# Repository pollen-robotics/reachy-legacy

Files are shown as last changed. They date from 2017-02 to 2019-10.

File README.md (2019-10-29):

# Reachy the Bio-Inspired Robotic Arm

**Beautiful, Easy-to-use, Versatile, Open Source Human-size robotic arm for your robotic applications!**

## About
Reachy is a unique robot arm with a high level of mobility (7-Dofs). Different tool can be added on the arm's tip such as hook, gripper and 5 fingers hand.
You can learn more about this project on [its webpage](https://www.pollen-robotics.com/en/our-products/reachy/) and on youtube:
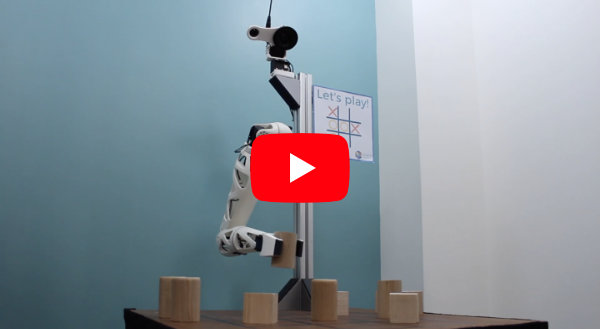
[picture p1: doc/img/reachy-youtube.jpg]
Video preview (https://www.youtube.com/watch?v=wsCYkz-BHyA&list=PLoZg6JOJfhpCa1Sy3cM4FOFkcFUBElqBF&index=2)


Reachy is designed and produced by Pollen Robotics, we offer product design and custom developpement, you can learn more on our [website](https://www.pollen-robotics.com/).

## Open source
Reachy hardware and software are both open source and can be freely modified/custumized by the end user to fit its needs.

The software is built on top of the [Pypot library](https://github.com/poppy-project/pypot) and is distributed under LGPL Licence.

The hardware is made using OnShape under [Creative Commons BY-SA licence](https://creativecommons.org/licenses/by-sa/4.0/) licence and is accessible [here](https://cad.onshape.com/documents/66388ae9c63cef53d76acd77/w/68c2411483d5bc65c7f54234/e/581d46ba9b8ee98de9d636ee)

## Documentation
In this repository, there are multiple examples explaining how to use reachy.

- A Quickstart on how to plug and start reachy can be found [here](./doc/readme.md).
- You can learn more on the software architecture [here](./doc/reachy-software-presentation.ipynb).
- Several examples are available in the folder [applications](./applications/).

Those notebooks can be viewed directly on GitHub or can also be run locally to directly experiment with your robot. See the [jupyter documention](https://jupyter.org) for mor information on how to do that.

## Installation

Reachy's control library is written in Python (>=2.7 or >= 3.4) and works on Win/Mac/Linux and Raspberry Pi. It allows for fast and simple control of your robotic arm. And also provides you example with more advanced features such as inverse kinematics, simulation, tracking, etc. It relies on the [pypot library](https://github.com/poppy-project/pypot) for the dynamixel motor communication.

On Raspberry-Pi, you can burn a ready to use image file (installation for both Python2 and Python3): [here](https://github.com/pollen-robotics/reachy/releases). You will need a 16Go SD card. 
You can plug a screen and keyboard directly on the Raspberry Pi or you can access it via ssh (hostname *reachy*, user *pi* and password *reachy*).

It can be installed from the source via pip.

```
git clone https://github.com/pollen-robotics/reachy.git
pip install -e ./reachy/software
```

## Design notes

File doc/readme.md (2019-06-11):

# Quickstart with Reachy

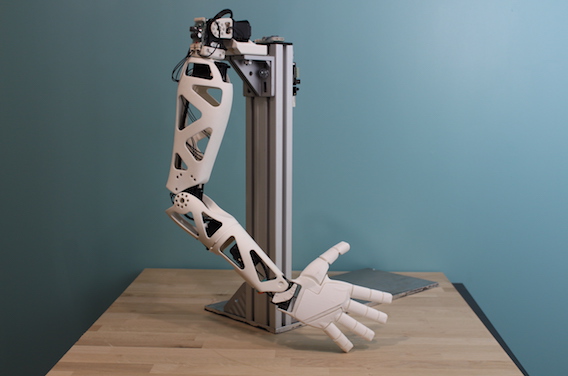
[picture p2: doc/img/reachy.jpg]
Reachy


## Plug your Reachy

The first step to start your Reachy robot is to make sure the motors are powered using the **two dedicated 12V power supply**. The usb dongle used to connect to the motors should be plugged to your computer or the Raspberry Pi.

See the pictures below for details.

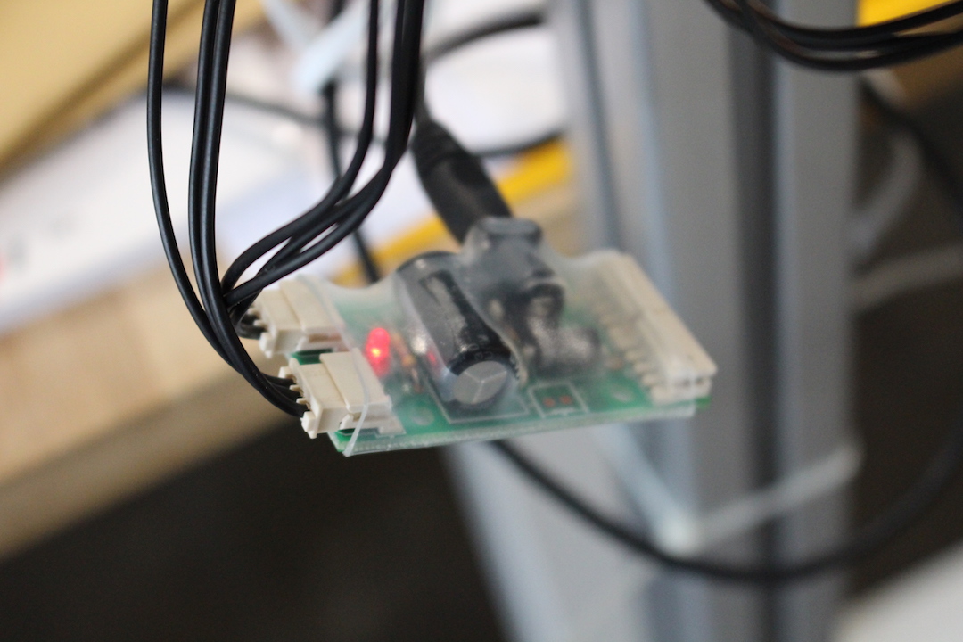
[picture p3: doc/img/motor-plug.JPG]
Motor plug

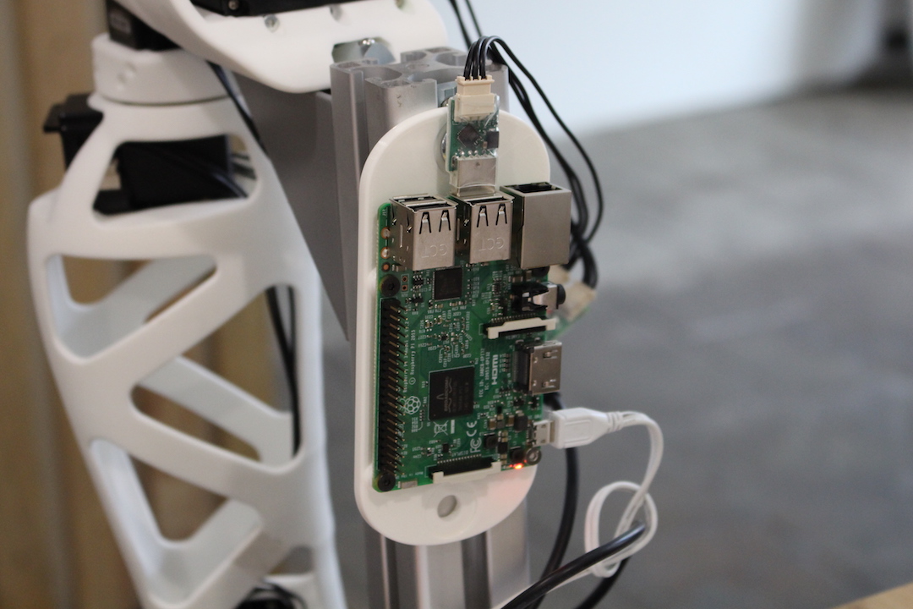
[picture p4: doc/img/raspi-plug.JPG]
Raspberry plug


Depending on the end-effector you are using, you may also need to plug it. For instance, also plug the dedicated USB if you are using the gripper with the force sensor.

## Software

The control libraries used for Reachy are all written in Python and can be directly found in this repo. A complete presentation can be found [here](./reachy-software-presentation.ipynb). You can also read the [Quickstart](./notebook/Reachy-Quickstart.ipynb) to directly jump in controlling reachy.

Most of the documentation can be found as jupyter notebook. Make sure to check [their documentation](https://jupyter.org) if you are unfamiliar with them. They are a really powerful way to document and let you experiment code.
You will find them in two main places:

* the basic ones for a general presentation can be found [here](./notebook).
* the specific ones with which are more applications oriented can be found [here](../applications)

## Safety First

Using a Reachy is not complex but at first it is easy to get confused. Most of the times it is not a big deal but some of the incorrect uses may easily damage it. There are a few pitfalls to avoid that, that can really help you at the beginning.

We strongly recommend you to have a look at the [safety first notebook](Safety-first.ipynb) to make sure everything goes well with your robot. By following these simple rules, you will be able to have your robot running without problem.

## FAQ & Troubleshooting

* Most of the connection problem with the robot are due to broken or badly plugged motor wires. Make sure to check them when you have trouble controlling your robot.

* Make sure to set the motor to not compliant before trying to move them! Otherwise they will simply do nothing.

* You can find more information on the documentation of the poppy project: https://docs.poppy-project.org/
 Most code should also work for the Reachy robot.

## Appendix - Using the Raspberry-Pi webinterface

### Connect to the robot interface

Once the robot is started, you can connect to its web interface. You can directly access it on http://reachy.local/ (This uses the zeroconf protocol to resolve the hostname. It should directly works on Linux and OS-X but requires to install this on Windows: https://support.apple.com/kb/DL999 You can also directly use the robot's IP if you know it).

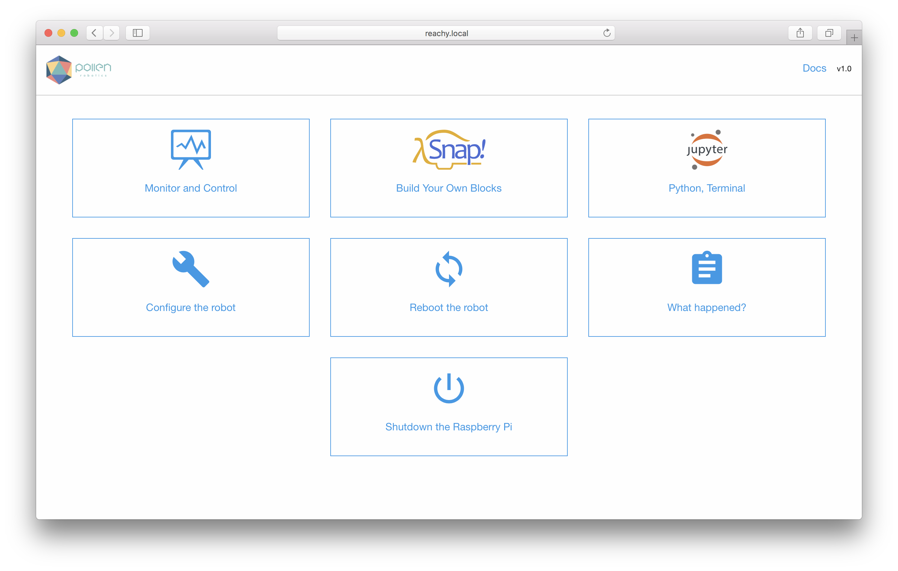
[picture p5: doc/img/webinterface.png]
Reachy web interface


 This lets you to use the monitor interface, directly run Python code in your robot using Jupyter or use the visual language Snap.

 You can find an example of Python code to start making your robot move in Jupyter.

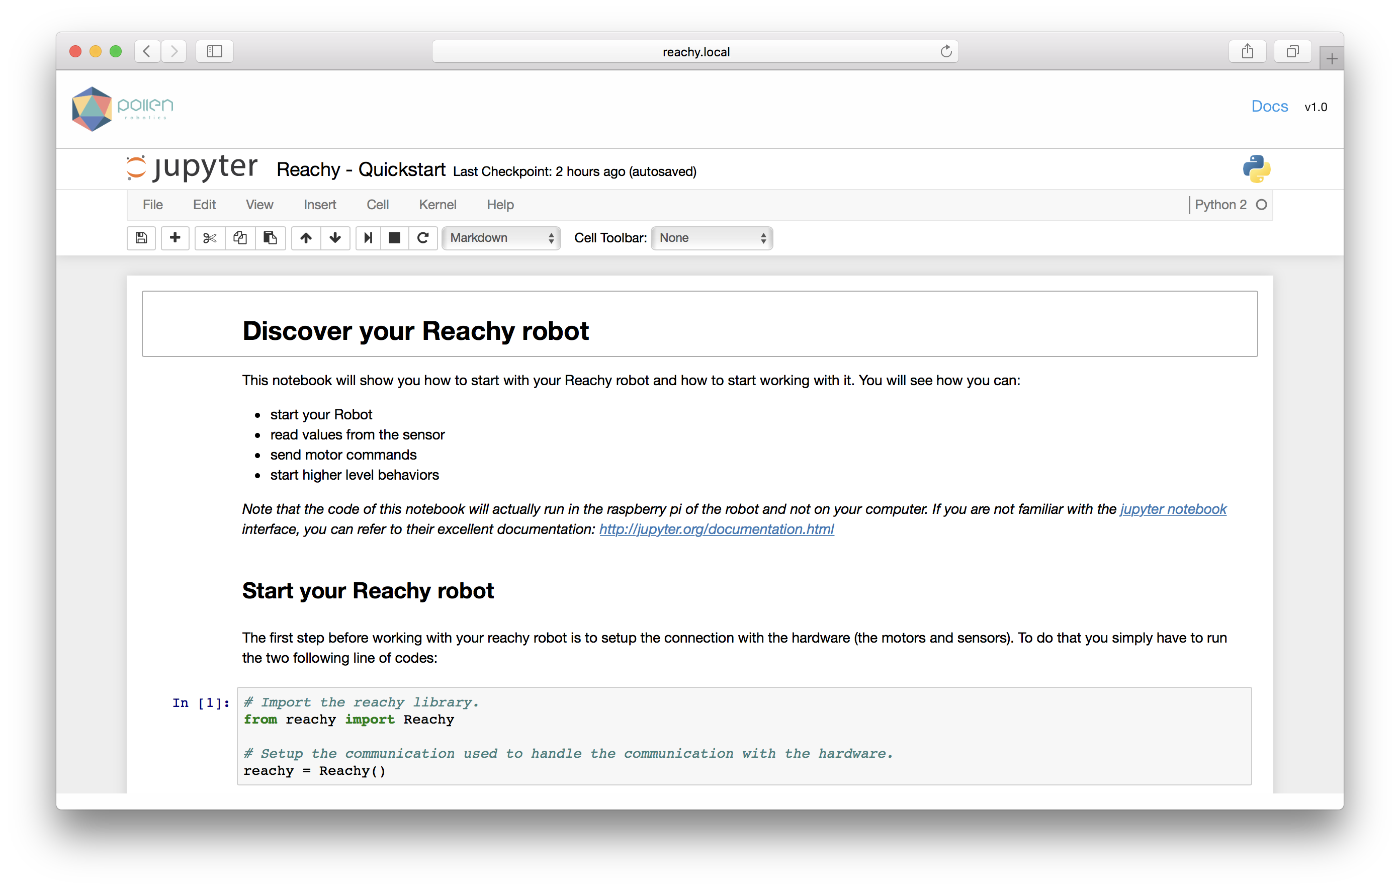
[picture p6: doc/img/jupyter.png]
Reachy jupyter example


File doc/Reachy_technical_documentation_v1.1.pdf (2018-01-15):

REACHY technical documentation

## REACHY TECHNICAL DOCUMENTATION

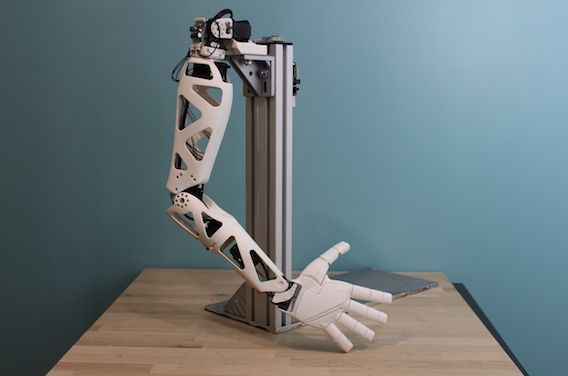
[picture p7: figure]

REACHY technical documentation

REVISIONS

Date | Revision | Author(s) | Comment(s)
22/11/2017 | 1.0 | Simon BAUDRY | First draft. Work in progress
15/01/2018 | 1.1 | Simon BAUDRY | New dimension specs.

REACHY technical documentation

# SUMMARY

### 1. Introduction

### 2. General specifications

### 3. Joints’ specifications

### 4. Dimensions

### 5. Initial position

### 6. Joints’ rotation

### 7. Servo-motors’ specifications

REACHY technical documentation

# 1.Introduction

Reachy is a full-size 7-dof prosthetic robotic arm. It can be programmed intuitively by demonstration or via an easy-to-use programming library.
It provides direct and inverse kinematics.

REACHY technical documentation

# 2.General specifications

Weight: ~1400 g

Height: ~660 mm to ~800 mm (according to type of hand).

Degrees of freedom: 7

Power requirement:
Minimum one power supply 12V 5A. Suggested two power supplies 12V 5A (one for the upper motor in the shoulder, one for the other motors in the arm).

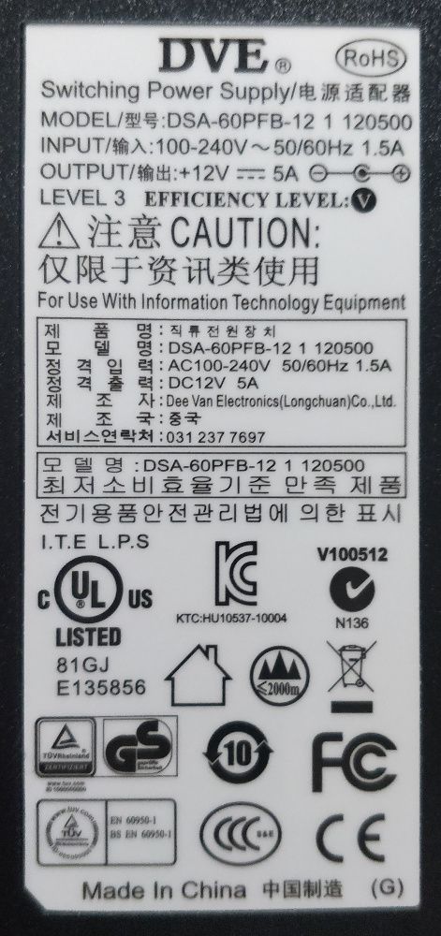
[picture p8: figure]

REACHY technical documentation

Payload:
WIP

Fixation method:
The arm can be fixed to a T-slotted bar.

Reproducibility of movements and delta: WIP

REACHY technical documentation

# 3.Joints’ specifications

Reachy is divided in 5 parts and 7 joints.

A part is composed of an actuator and a shell. Parts are roughly the same than in human body (e.g. shoulder, wrist, …).
A joint is the location where a motion is allowed (e.g. rotation point between forearm and wrist); each joint is associated to a degree of freedom.

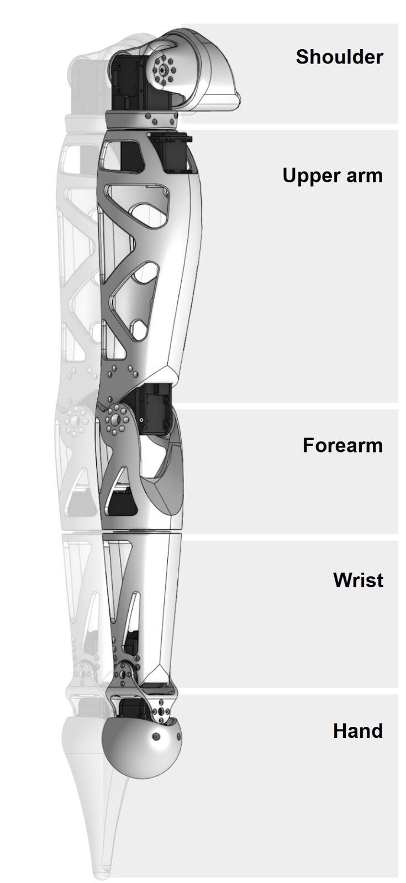
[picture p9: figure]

REACHY technical documentation

# 4.Dimensions

Dimensions on the top in the figure X and left of the figure Y below are provided from one rotation point (joint) to another. Dimensions on the bottom and on the right are general maximal dimensions (according to two different types of hand).

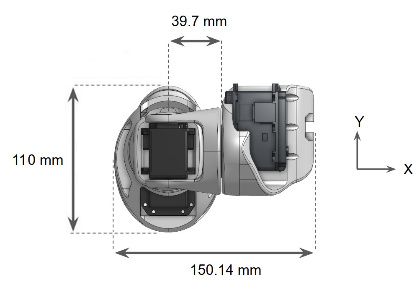
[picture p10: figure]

REACHY technical documentation

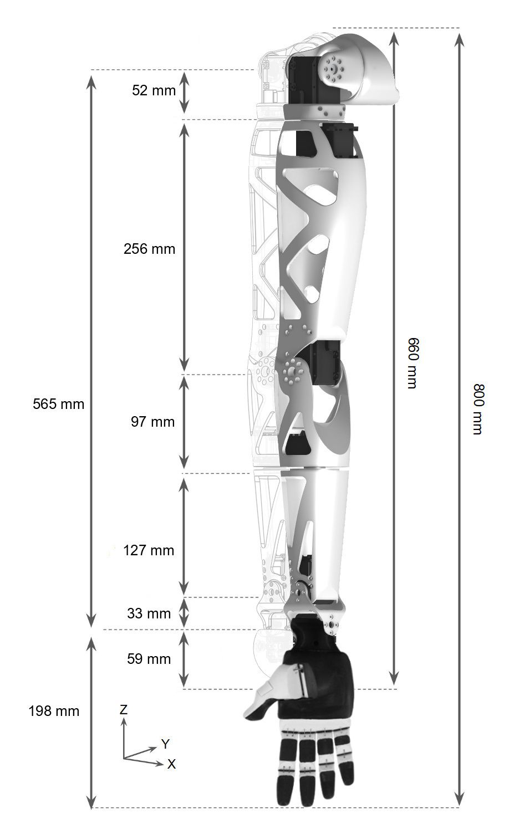
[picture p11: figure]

REACHY technical documentation

# 5.Initial position

Reachy’s initial position is as shown:

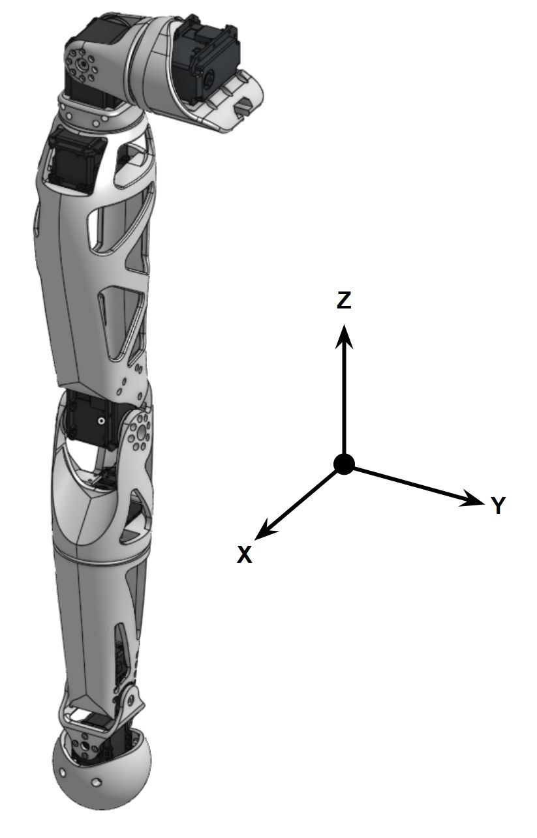
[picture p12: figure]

REACHY technical documentation

# 6.Joints’ rotation

Each joint rotates around an axis, based from 0-position of Reachy. A rotation around X axis is called Roll, a rotation around Y axi is called Pitch, and a rotation around Z axis is called Yaw.

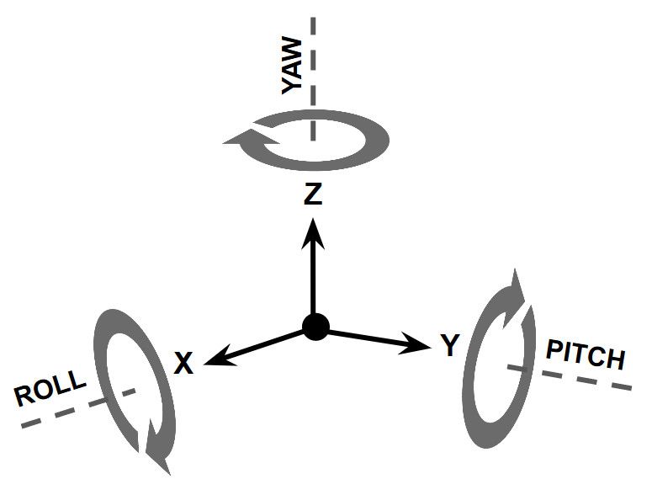
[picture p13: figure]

According to this, the joint’s names are composed of the place of the joint (shoulder, elbow, ...) and the rotation allowed (pitch, roll, or yaw). Each joint has a limited range angle (no endless rotation).

REACHY technical documentation

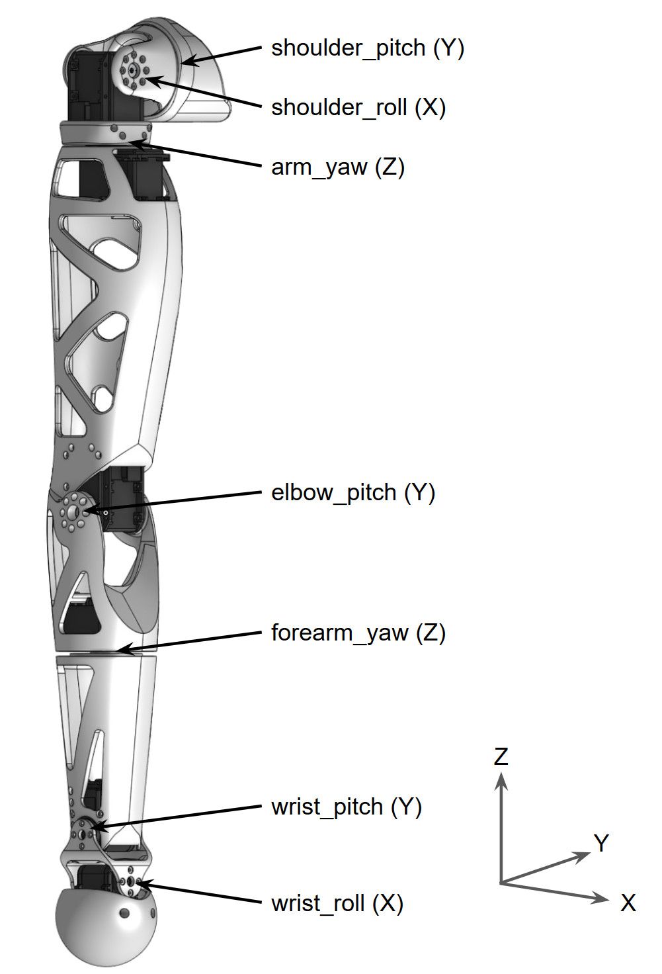
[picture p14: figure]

The following tables show servo-motors’ name, ranges of angles and initial angle of each joint.

REACHY technical documentation

| Right arm
Motor type | Origin angle ° | Min angle ° | Max angle °
shoulder_pitc h | MX-106T | -90 | -180 | 90
shoulder_roll | MX-64AT | -90 | -100 | 90
arm_yaw | MX-64AT | 0 | -90 | 90
elbow_pitch | MX-64AT | 0 | 0 | 125
forearm_yaw | AX-18A | 0 | -150 | 150
wrist_pitch | AX-18A | 0 | -70 | 70
wrist_roll | AX-18A | 0 | -60 | 60
| Left arm
Motor type | Origin angle ° | Min angle ° | Max angle °
shoulder_pitc h | MX-106T | -90 | -180 | 90
shoulder_roll | MX-64AT | -90 | -100 | 90
arm_yaw | MX-64AT | 0 | -90 | 90
elbow_pitch | MX-64AT | 0 | 0 | 125
forearm_yaw | AX-18A | 0 | -150 | 150
wrist_pitch | AX-18A | 0 | -70 | 70
wrist_roll | AX-18A | 0 | -60 | 60

REACHY technical documentation

# 7.Servo-motors’ specifications

Servo-motors are from the company Robotis, Dynamixel type.

| Resolution ° | Dimension LxDxH mm | Weight g | Running degrees ° | Reduction ratio | Link
MX-106T | 0.088 | 40.2x65.1x46 | 153 | 0-360, endless | 225 | TTL
MX-64AT | 0.088 | 40.2x61.1x41 | 135 | 0-360, endless | 200
AX-18A | 0.29 | 32x50x40 | 54.5 | 0-300, endless | 254
| Voltage | Stall torque (N.m) | No-load speed (RPM) | Stall current (A) | Standby current
Range (V) | (V) | 11.1V | 12V | 14.8V | 11.1V | 12V | 14.8V | 11.1V | 12V | 14.8V | mA Nominal
MX-106T | 10-14.8 | 12 | 8 | 8.4 | 10 | 41 | 45 | 55 | 4.8 | 5.2 | 6.3 | 100
MX-64AT | 10-14.8 | 12 | 5.5 | 6 | 7.3 | 58 | 63 | 78 | 3.9 | 4.1 | 5.2 | 100
AX-18A | 9-12 | 11.1 | - | 1.8 | - | - | 97 | - | - | 2.2 | - | -

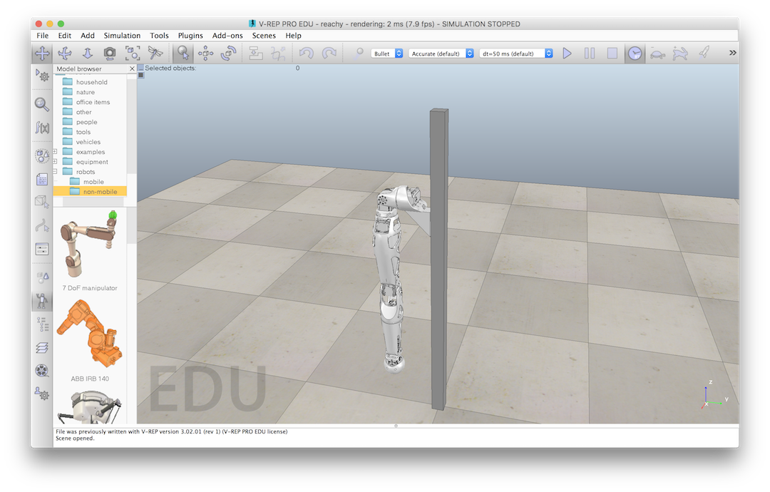
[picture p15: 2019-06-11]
doc/img/reachy-vrep.png

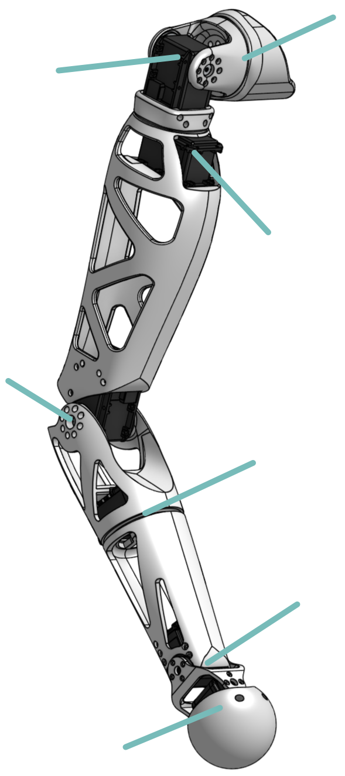
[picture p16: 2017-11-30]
assets/reachy.png

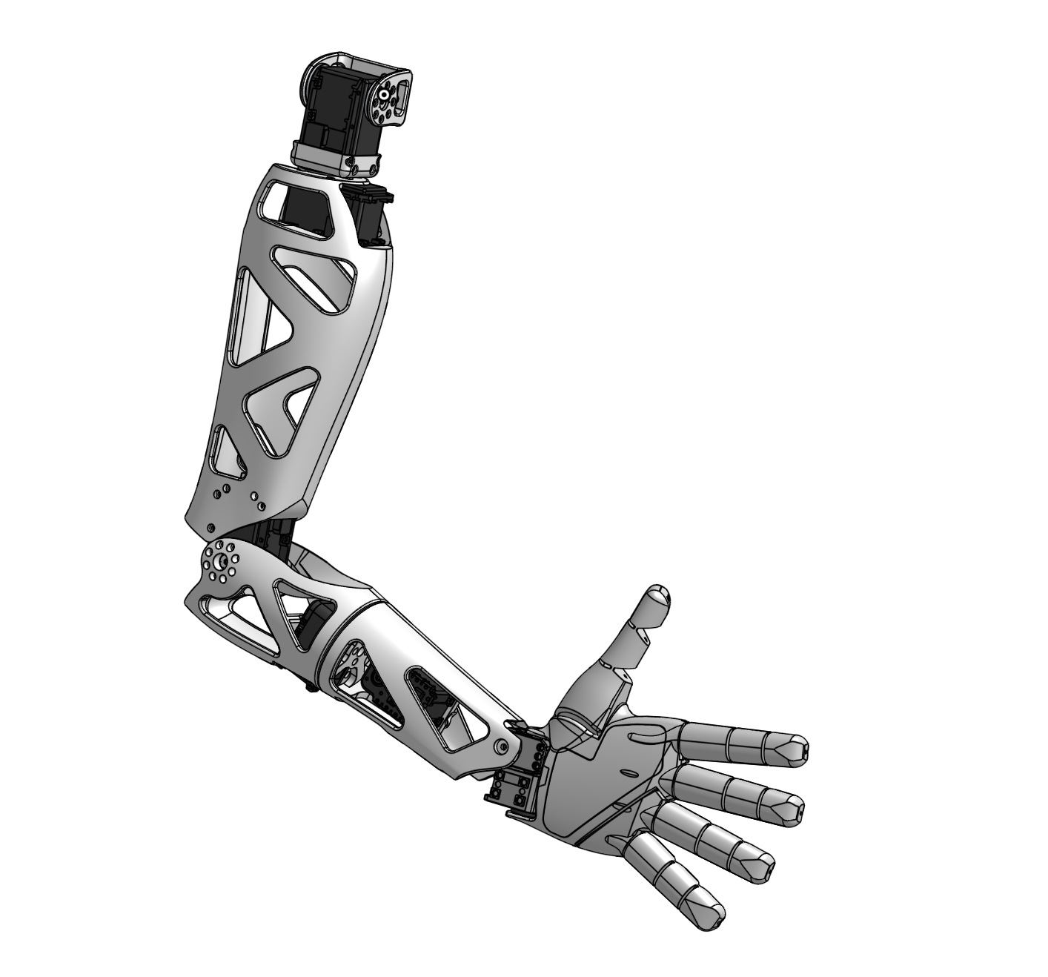
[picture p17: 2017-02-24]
doc/img/meca.png

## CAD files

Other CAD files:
hardware/URDF/meshes/trunk-respondable.stl
hardware/URDF/meshes/open_bionics_hand_left-visual.stl
hardware/URDF/meshes/open_bionics_hand_right-visual.stl
hardware/URDF/meshes/head_u-visual.stl
hardware/URDF/meshes/head-eyes-visual.stl
hardware/URDF/meshes/trunk-visual.stl
hardware/URDF/meshes/open_bionics_hand_left-respondable.stl
hardware/URDF/meshes/head-eyes-respondable.stl
hardware/URDF/meshes/open_bionics_hand_right-respondable.stl
hardware/URDF/meshes/shoulder-left-visual.stl
hardware/URDF/meshes/shoulder-y-left-respondable.stl
hardware/URDF/meshes/shoulder-y-left-visual.stl
hardware/URDF/meshes/shoulder-left-respondable.stl
hardware/URDF/meshes/forearm-respondable.stl
hardware/URDF/meshes/forearm-visual.stl
hardware/URDF/meshes/ball-tip-respondable.stl
hardware/URDF/meshes/shoulder-y-respondable.stl
hardware/URDF/meshes/wrist-hand-visual.stl
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

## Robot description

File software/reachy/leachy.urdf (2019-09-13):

<?xml version="1.0"?>
<robot name="Reachy">

  <material name="blue">
    <color rgba="0 0 0.8 1"/>
  </material>

  <material name="white">
    <color rgba="1 1 1 1"/>
  </material>

  <material name="red">
    <color rgba="0.8 0 0 1"/>
  </material>

<link name="base">
    <visual>
      <geometry>
        <mesh filename="package://meshes/shoulder-y-left-visual.STL"></mesh>
      </geometry>
      <material name="blue"/>
    </visual>
    <inertial>
      <inertia ixx= "1.043e-4" ixy= "6.147e-6" ixz= "-1.971e-6" iyy= "1.364e-4" iyz= "1.466e-5" izz= "1.403e-4" ></inertia>
      <mass value="0.221"></mass>
    </inertial>
    <collision>
      <origin xyz="0 0 0" rpy="0 0 0"></origin>
      <geometry>
        <mesh filename="package://meshes/shoulder-y-left-respondable.STL"></mesh>
      </geometry>
    </collision>
  </link>

  <link name="shoulder">
    <visual>
      <origin xyz="0 0 0" rpy="0 0 0"></origin>
      <geometry>
        <mesh filename="package://meshes/shoulder-left-visual.STL"></mesh>
      </geometry>
      <material name="white"/>
    </visual>
    <inertial>
      <inertia ixx= "1.299e-5" ixy= "5.557e-10" ixz= "-2.973e-10" iyy= "2.323e-5" iyz= "-8.199e-8" izz= "2.227e-5" ></inertia>
      <mass value="0.036"></mass>
    </inertial>
    <collision>
      <origin xyz="0 0 0" rpy="0 0 0"></origin>
      <geometry>
        <mesh filename="package://meshes/shoulder-left-respondable.STL"></mesh>
      </geometry>
    </collision>

  </link>

  <link name="shoulder_to_arm">
    <visual>
      <geometry>
        <mesh filename="package://meshes/shoulder-x-visual.STL"></mesh>
      </geometry>
      <origin rpy="0 0 0" xyz="0 0 0"/>
      <material name="blue"/>
    </visual>
    <inertial>
      <inertia ixx= "6.811e-5" ixy= "-2.299e-10" ixz= "-4.502e-7" iyy= "7.593e-5" iyz= "-1.674e-9" izz= "4.248e-5" ></inertia>
      <mass value="0.155"></mass>
    </inertial>
    <collision>
      <origin xyz="0 0 0" rpy="0 0 0"></origin>
      <geometry>
        <mesh filename="package://meshes/shoulder-x-respondable.STL"></mesh>
      </geometry>
    </collision>
  </link>

  <link name="upper_arm">
    <visual>
      <geometry>
        <mesh filename="package://meshes/upper-arm-visual.STL"></mesh>
      </geometry>
      <origin rpy="0 0 0" xyz="0 0 0"/>
      <material name="white"/>
    </visual>
    <inertial>
      <inertia ixx= "4.171e-3" ixy= "1.333e-7" ixz= "-2.900e-4" iyy= "4.276e-3" iyz= "1.465e-6" izz= "3.177e-4" ></inertia>
      <mass value="0.430"></mass>
    </inertial>
    <collision>
      <origin xyz="0 0 0" rpy="0 0 0"></origin>
      <geometry>
        <mesh filename="package://meshes/upper-arm-respondable.STL"></mesh>
      </geometry>
    </collision>
  </link>

  <link name="forearm">
    <visual>
      <origin xyz="0 0 0" rpy="0 0 0"></origin>
      <geometry>
        <mesh filename="package://meshes/forearm-visual.STL"></mesh>
      </geometry>
      <origin rpy="0 0 0" xyz="0 0 0"/>
      <material name="blue"/>
    </visual>
    <inertial>
      <inertia ixx= "1.724e-4" ixy= "-1.733e-8" ixz= "1.854e-5" iyy= "1.815e-4" iyz= "-4.191e-8" izz= "9.299e-5" ></inertia>
      <mass value="0.129"></mass>
    </inertial>
    <collision>
      <origin xyz="0 0 0" rpy="0 0 0"></origin>
      <geometry>
        <mesh filename="package://meshes/forearm-respondable.STL"></mesh>
      </geometry>
    </collision>
  </link>

  <link name="wrist">
    <visual>
      <origin xyz="0 0 0" rpy="0 0 0"></origin>
      <geometry>
        <mesh filename="package://meshes/wrist-visual.STL"></mesh>
      </geometry>
      <origin rpy="0 0 0" xyz="0 0 0"/>
      <material name="white"/>
    </visual>
    <inertial>
      <inertia ixx= "2.215e-4" ixy= "-2.163e-8" ixz= "-4.702e-6" iyy= "2.306e-4" iyz= "-6.577e-7" izz= "5.075e-5" ></inertia>
      <mass value="0.115"></mass>
    </inertial>
    <collision>
      <origin xyz="0 0 0" rpy="0 0 0"></origin>
      <geometry>
        <mesh filename="package://meshes/wrist-respondable.STL"></mesh>
      </geometry>
    </collision>
  </link>

  <link name="wrist_hand">
    <visual>
      <geometry>
        <mesh filename="package://meshes/wrist-hand-visual.STL"></mesh>
      </geometry>
      <origin rpy="0 0 0" xyz="0 0 0"/>
      <material name="blue"/>
    </visual>
    <inertial>
      <inertia ixx= "3.861e-6" ixy= "-2.805e-9" ixz= "-8.067e-8" iyy= "3.694e-6" iyz= "-7.689e-8" izz= "4.987e-6" ></inertia>
      <mass value="0.009"></mass>
    </inertial>
    <collision>
      <origin xyz="0 0 0" rpy="0 0 0"></origin>
      <geometry>
        <mesh filename="package://meshes/wrist-hand-respondable.STL"></mesh>
      </geometry>
    </collision>

  </link>

  <link name="hand_ball">
    <visual>
      <geometry>
        <mesh filename="package://meshes/ball-tip-visual.STL"></mesh>
      </geometry>
      <origin rpy="0 0 0" xyz="0 0 0"/>
      <material name="white"/>
    </visual>
    <inertial>
      <inertia ixx= "4.177e-5" ixy= "2.340e-9" ixz= "3.492e-8" iyy= "4.290e-5" iyz= "-2.318e-11" izz= "3.596e-5" ></inertia>
      <mass value="0.090"></mass>
    </inertial>
    <collision>
      <origin xyz="0 0 0" rpy="0 0 0"></origin>
      <geometry>
        <mesh filename="package://meshes/ball-tip-respondable.STL"></mesh>
      </geometry>
    </collision>
  </link>

<!--   <link name="ball">
    <visual>
      <geometry>
        <sphere radius="0.02"/>
      </geometry>
      <origin rpy="0 0 0" xyz="0 0 0"/>
      <material name="red"/>
    </visual>
  </link> -->

  <joint name="l_shoulder_pitch" type="revolute">
    <parent link="base"/>
    <child link="shoulder"/>
    <origin rpy="0 0 0" xyz="0 0.14 0"/>
    <axis xyz="0 1 0"/>
    <limit lower="-1.5708" upper="3.14159"/>
  </joint>

  <joint name="l_shoulder_roll" type="revolute">
    <parent link="shoulder"/>
    <child link="shoulder_to_arm"/>
    <origin rpy="0 0 0" xyz="0 0 0"/>
    <axis xyz="1 0 0"/>
    <limit lower="-0.174533" upper="3.14159"/>
  </joint>

  <joint name="l_arm_yaw" type="revolute">
    <parent link="shoulder_to_arm"/>
    <child link="upper_arm"/>
    <origin rpy="0 0 0" xyz="0 0 0"/>
    <axis xyz="0 0 1"/>
    <limit lower="-1.5708" upper="1.5708"/>
  </joint>

  <joint name="l_elbow_pitch" type="revolute">
    <parent link="upper_arm"/>
    <child link="forearm"/>
    <origin rpy="0 0 0" xyz="0 0 -0.30745"/>
    <axis xyz="0 1 0"/>
    <limit lower="-2.18166" upper="0"/>
  </joint>

  <joint name="l_forearm_yaw" type="revolute">
    <parent link="forearm"/>
    <child link="wrist"/>
    <origin rpy="0 0 0" xyz="0 0 0"/>
    <axis xyz="0 0 1"/>
    <limit lower="-2.61799" upper="2.61799"/>
  </joint>

  <joint name="l_wrist_pitch" type="revolute">
    <parent link="wrist"/>
    <child link="wrist_hand"/>
    <origin rpy="0 0 0" xyz="0 0 -0.22415"/>
    <axis xyz="0 1 0"/>
    <limit lower="-1.22173" upper="1.22173"/>
  </joint>

  <joint name="l_wrist_roll" type="revolute">
    <parent link="wrist_hand"/>
    <child link="hand_ball"/>
    <origin rpy="0 0 0" xyz="0 0 -0.03243"/>
    <axis xyz="1 0 0"/>
    <limit lower="-1.0472" upper="1.0472"/>
  </joint>

</robot>

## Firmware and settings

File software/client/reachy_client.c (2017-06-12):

#include <math.h>
#include <stdio.h>
#include <unistd.h>

#include "zhelpers.h"


int main() {
  void *context = zmq_ctx_new();
  void *client = zmq_socket(context, ZMQ_REQ);

  // Connects to the robot server.
  zmq_connect(client, "tcp://reachy.local:9898");
  printf("Connecting to reachy...\n");

  // Read the position of one motor: "shoulder_roll".
  char *pos_cmd = "{\"robot\": {\"get_register_value\": {\"motor\": \"shoulder_roll\", \"register\": \"present_position\"}}}";
  s_send(client, pos_cmd);
  printf("Shoulder roll current position: %s\n", s_recv(client));

  // Read the speed of one motor: "shoulder_roll".
  char *speed_cmd = "{\"robot\": {\"get_register_value\": {\"motor\": \"shoulder_roll\", \"register\": \"present_speed\"}}}";
  s_send(client, speed_cmd);
  printf("Shoulder roll current speed: %s\n", s_recv(client));

  // Set the "shoulder_roll" motor to stiff (not compliant).
  char *compliant_cmd = "{\"robot\": {\"set_register_value\": {\"motor\": \"shoulder_roll\", \"register\": \"compliant\", \"value\": \"false\"}}}";
  s_send(client, compliant_cmd);
  printf("Shoulder roll is now stiff (error: %s)\n", s_recv(client));

  // Set the "shoulder_roll" motor goal maximum speed to 50rpm.
  char *max_speed_cmd = "{\"robot\": {\"set_register_value\": {\"motor\": \"shoulder_roll\", \"register\": \"moving_speed\", \"value\": \"50\"}}}";
  s_send(client, max_speed_cmd);
  printf("Shoulder roll max speed is now moving 50 (error: %s)\n", s_recv(client));

  // Set the "shoulder_roll" motor goal position to 45.
  char *move_cmd = "{\"robot\": {\"set_register_value\": {\"motor\": \"shoulder_roll\", \"register\": \"goal_position\", \"value\": \"45\"}}}";
  s_send(client, move_cmd);
  printf("Shoulder roll is now moving to position 45 (error: %s)\n", s_recv(client));

  sleep(3);

  // Set the "shoulder_roll" motor goal position back to 0.
  char *back_cmd = "{\"robot\": {\"set_register_value\": {\"motor\": \"shoulder_roll\", \"register\": \"goal_position\", \"value\": \"0\"}}}";
  s_send(client, back_cmd);
  printf("Shoulder roll is now moving to position 0 (error: %s)\n", s_recv(client));

  sleep(3);

  // Make the "arm_yaw" motor follows a sinusoid for 5s.
  // First we set it to stiff mode.
  char *stiff_cmd = "{\"robot\": {\"set_register_value\": {\"motor\": \"arm_yaw\", \"register\": \"compliant\", \"value\": \"false\"}}}";
  s_send(client, stiff_cmd);
  s_recv(client);

  float freq = 0.5;
  float amp = 30;
  int period = 20 * 1000; // we update position every 20ms
  int duration = 5;
  int steps = 50 * duration;

  char cmd[256];
  char *sin_cmd = "{\"robot\": {\"set_register_value\": {\"motor\": \"arm_yaw\", \"register\": \"goal_position\", \"value\": \"%g\"}}}";
  char *get_cmd = "{\"robot\": {\"get_register_value\": {\"motor\": \"arm_yaw\", \"register\": \"present_position\"}}}";

  // Then we affect new pos every 20ms.
  for (float t=0; t < duration; t += 0.02) {
    float pos = amp * sin(2 * M_PI * freq * t);

    snprintf(cmd, sizeof(cmd), sin_cmd, pos);
    s_send(client, cmd);
    s_recv(client);

    s_send(client, get_cmd);
    printf("Current pos %s Goal pos %g\n", s_recv(client), pos);

    usleep(period);
  }

  return 0;
}

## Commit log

2017-02-10 Update reachy config.
    Changes the forearm_grip from wheel mode to joint mode.
2017-10-18 URDF build by hand that seems correct: - tested visually on https://mymodelrobot.appspot.com/5629499534213120 - distances and measurement extracted from OnShape
    [reachy.URDF]
2017-10-19 Add URDF import test in Ikpy.
2017-10-19 Typo in URDF path.
2017-10-19 Add rpy to all joints
    [reachy.URDF]
2017-10-19 added axis to shoulder_pitch removed ball_joint joint not handled by ikpy
    [reachy.URDF]
2017-10-19 axis corrected for shoulder_pitch added limit to all joints
    [reachy.URDF]
2017-10-19 Add kinematic notebook example.
2017-10-24 Fix motor orientation in config.
2017-11-28 modification of the URDF to fit the axis convention
    [reachy.URDF]
2017-11-28 add Reachy Left aka Leachy configuration and URDF
    [leachy.URDF]
2017-11-28 Update notebook irw new URDF.
2017-11-28 Remove deprecated non joint motors.
2017-11-29 Fix URDF path in notebook.
2018-04-04 add visual and respondable 3D shapes
    [ball-tip-respondable.stl, ball-tip-visual.stl, forearm-respondable.stl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]
2018-04-04 update URDF with 3D models
    [reachy.URDF]
2018-04-09 Fix timer script in vrep scene.
2018-04-09 Install urdf.
    [leachy.urdf, reachy.urdf]
2018-04-09 Add ik chain wrapper.
2018-04-12 update leachy URDF with 3D shapes
    [leachy.URDF, leachy.urdf, shoulder-left-respondable.stl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]
2018-04-12 update reachy scene with new PID, joint orientation and limits
2018-04-22 v-rep model fix reachy shoulder joint orientation
2018-04-24 Use new motor name with specific r_ or l_ prefix.
    [leachy.urdf, reachy.urdf]
2018-05-29 Fix kinematics angles conversion.
2018-09-19 add URDF for IK with hand
    [leachy-hand.URDF]
2018-09-19 Update ik with brunel hand.
    [leachy_hand.urdf]
2018-09-19 Add notebook with visual servoing.
2018-09-26 fix orientation bug in the reachy wrist joint
2018-09-26 Improve kinematics API.
2019-05-29 Add notebook example of use of the force gripper.
2019-06-11 add lua timer code for vrep simulation
2019-06-11 add 2 power supply
2019-09-13 Fix urdf file.
    [leachy.urdf, leachy_hand.urdf, reachy_hand.urdf]
2019-09-17 Prevent a bug when importing vrep with raspberry pi.
2019-09-23 Add URDF Files and meshes for a Full Reachy with 2 arms, 2 open bionics hand and a head.
    [full-reachy-w-open-bionics.URDF, head-eyes-respondable.stl, head-eyes-visual.stl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]
2019-10-29 Set 55°C as the highest temperature for motors.
